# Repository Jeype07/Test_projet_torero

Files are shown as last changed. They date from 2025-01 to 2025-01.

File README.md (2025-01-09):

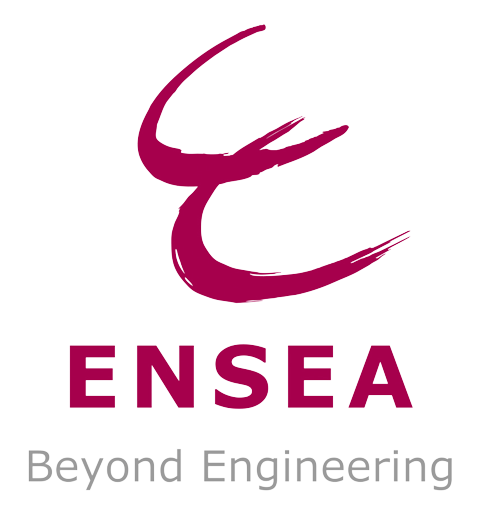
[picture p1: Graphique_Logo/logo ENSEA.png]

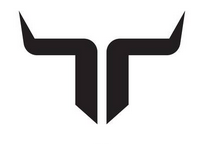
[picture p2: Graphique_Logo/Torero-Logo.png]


# 2425_ESE_Projet_Torero

## Projet de ESE de 3éme année de JACQUOT Nolan, GUIFFAULT Gabriel, BOULOT Paul et THOMAR Jean-Philippe

Ce projet contient toute les ressources de l'élaboration d'un robot capable de jouer au chat et a la souris.
Les liens vers les differentes ressources sont énuméré avec un court intitulé a la FIN du README.
Ci dessous le schéma architectural donnant les grandes lignes du projet.
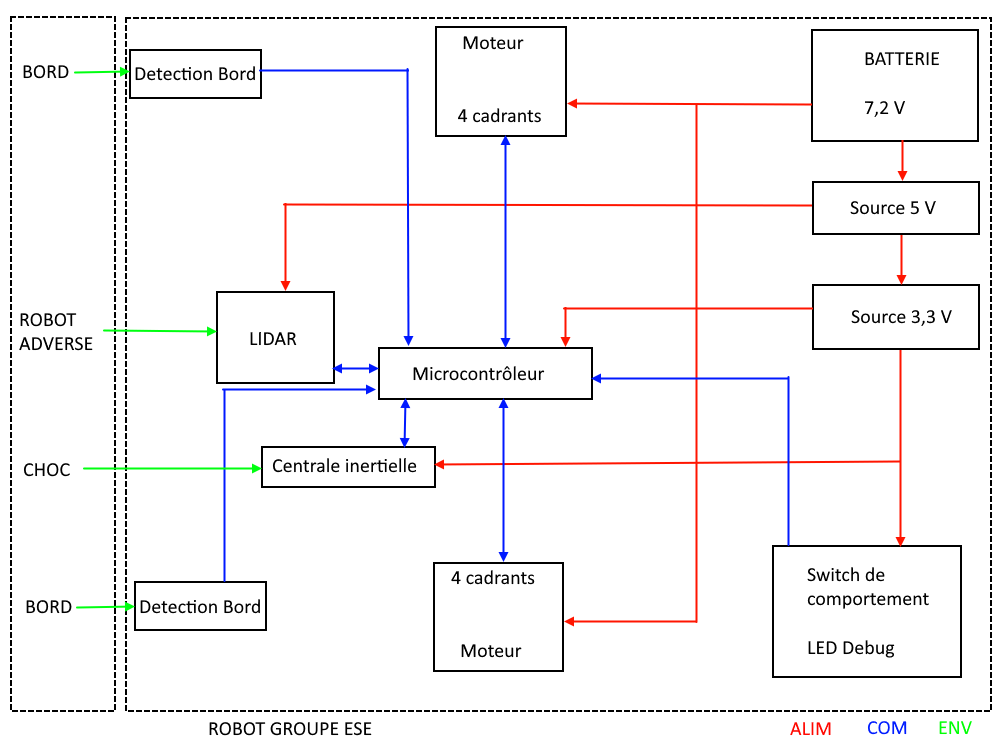
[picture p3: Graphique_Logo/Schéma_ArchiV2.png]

[Schéma architectural](https://github.com/user-attachments/files/17220902/Schema.architectural.pdf)

## Environnement:

> [!IMPORTANT]
> Table de 200cm x 160cm
> 
> Table sans Bord ni marquages!
> 
> Robot assimilable a un cylindre de 17 cm de diametre et 15 cm de hauteur 

## Cahier des charges:
> [!IMPORTANT]
>- Le robot doit etre capable de ce déplacer sur une table sans tomber (absence de bord et de marquage)
>- Le robot doit etre capable de detecter l'autre robot present sur la table pour le fuir ou le chasser en fonction de son role dans la partie.
>- Le robot doit etre capable de detecter un contact meme leger avec le robot adverse et changer son comportement d'un role vers l'autre.

Objectif annexe:
- Le robot peut realiser une odometrie simple pour suivre le bord de table lorsqu'il debute en souris
- Le robot peut realiser une odometrie simple pour se positionner au centre de la table avant de commencer la traque lorsqu'il debute en chat
- Le robot peut declencher un brusque changement de direction si il detecte un robot approchant rapidement en mode souris
- Le robot peut effectuer des prédiction de trajectoire et effectuer des trajectoires de collision en prévision du deplacement adverse en mode chat
- Le robot evite de prendre des directions ou il serait acculé dans un angle de table

### Dossier contenant les Datasheets : 
https://github.com/Manassehalt/2425_ESE_Projet_Torero/tree/main/Datasheet

### LISTE des choses faite ou a faire : 
https://github.com/Manassehalt/2425_ESE_Projet_Torero/blob/main/Calculs%20et%20brouillons/Remarque_Sch.md

### Lien utile : 
https://github.com/Manassehalt/2425_ESE_Projet_Torero/blob/main/Calculs%20et%20brouillons/Liens.xlsx

### BOM : 
https://github.com/Manassehalt/2425_ESE_Projet_Torero/blob/main/BOM.xlsx

### INFO PCB : 
https://github.com/Manassehalt/2425_ESE_Projet_Torero/blob/main/PCB/info_PCB.docx

### Apercu serigraphie :
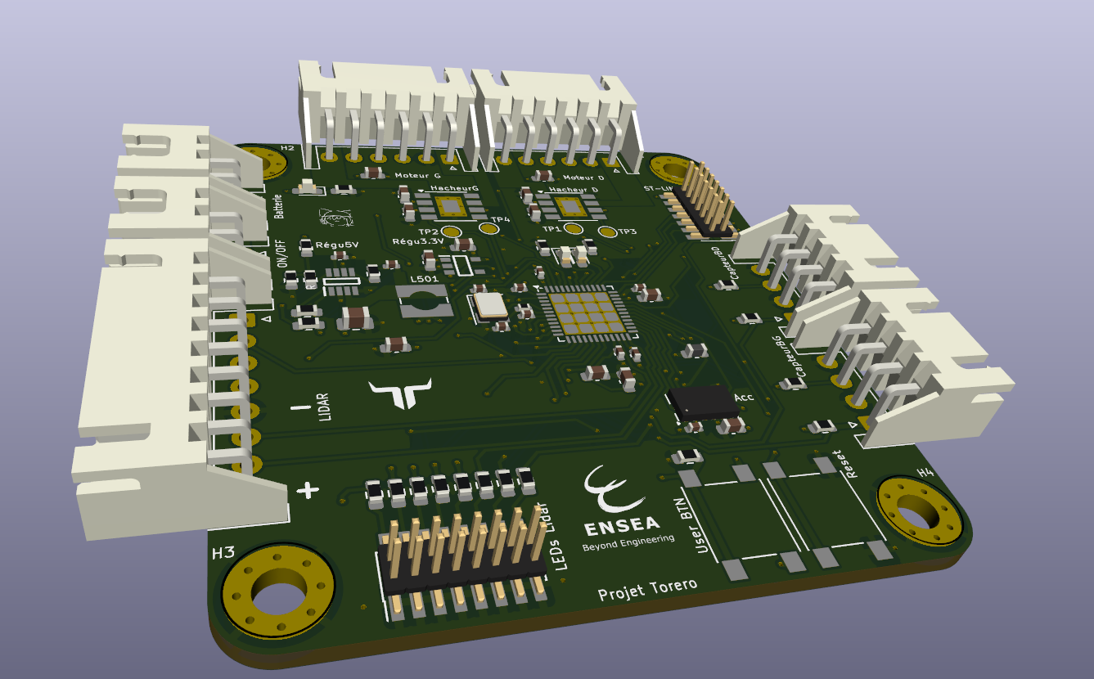
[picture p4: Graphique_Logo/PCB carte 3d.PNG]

[view PCB 3D](https://github.com/Manassehalt/2425_ESE_Projet_Torero/blob/main/Graphique_Logo/PCB%20carte%203d.PNG)

### DOSSIER PCB : 
https://github.com/Manassehalt/2425_ESE_Projet_Torero/tree/main/PCB

### Shematics_torero : 
https://github.com/Manassehalt/2425_ESE_Projet_Torero/blob/main/PCB/Projet_torero/Projet_torero.kicad_sch

### DOSSIER CODE STM32 : 
https://github.com/Manassehalt/2425_ESE_Projet_Torero/tree/main/Projet_ESE_STM32/Projet_ESE_Torero/STM32G431CBU6

### DOSSIER CALCULS : 
https://github.com/Manassehalt/2425_ESE_Projet_Torero/tree/8892ed05e16a1e8a040fe9dc08f9f57ab23dc9e8/Calculs%20et%20brouillons

### Methode si nouvel ordinateur : 
> [!TIP]
>Générer une clé SSH
>- Taper ssh-keygen puis Entrer
>- Appuyer sur y pour overwrite et sur Entrer pour passer les étapes (if no passphrase)
>- Taper cat ~/.ssh/id_ed25519.pub puis Entrer
>- Copier puis coller la clé dans GitHub Setting > SSH and GPG keys > SSH keys
>- Renommer avec le nom du PC pour savoir à quoi la clé correpond
>  ex : jeanp@HP-Pavilion-JP

### Ligne pour cloner un répertoire en utilisant le port 443 (https) au lieu du port 22, si bug sur la connexion:
> [!TIP]
>git clone ssh://git@ssh.github.com:443/username/Repositority_name.git

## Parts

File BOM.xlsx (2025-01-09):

NOM | REFERENCE | FOURNISSEUR | DESCRIPTION | PRIX UNITAIRE | QUANTITE | COUT TOTAL | STATUS COMMANDE | DATASHEET
STM32G431CBU6 |  |  | Microcontrôleur |  | 1 | 0.00 €
Quartz 16 MHz | 2853935 | Farnell |  |  | 1 | 0.00 €
Connecteur SWD/STLink | 3226055 | Farnell |  |  |  | 0.00 €
ZXBM5210-SP-13 |  |  | Driver moteur |  |  | 0.00 €
DfRobot FIT0520 ou FIT0521 |  |  | Moteurs |  | 2 | 0.00 €
ADXL343BCCZ-RL |  |  | Accéléromètre |  | 1 | 0.00 €
MP1475S |  |  | Régulateur 5V |  | 1 | 0.00 €
BU33SD5WG-TR |  |  | Régulateur 3.3V |  | 1 | 0.00 €
NIMH 7.2V 1.3Ah (RS : 777-0377) |  |  | Batterie 7.2V |  |  | 0.00 €
QRD1113 | 1467857/1467858 | Farnell | Capteur bordure |  | 2 | 0.00 €
YDLIDAR X4 |  |  | Lidar |  | 1 | 0.00 €
Connecteurs JST 2.54mm |  |  |  |  |  | 0.00 €
LED + R/C |  |  |  |  |  | 0.00 € | en 0603
Résistance 10 k |  |  | Résistance boot flash user button |  | 1
Capacité 20p |  |  |  |  | 2
Capacité 100n |  |  |  |  | 8
Capacité 1u |  |  |  |  | 9
Capacité 4n7 |  |  |  |  | 1
Capacité 10n |  |  |  |  | 1
Capacité 22u |  |  |  |  | 1
Capacité 47u |  |  |  |  | 1
Capacité 10u |  |  |  |  | 2
Diode rouge |  |  |  |  | 2
Diode verte |  |  |  |  | 1
Connecteur Pin header 2x7 1,27mm ST Link |  |  |  |  | 1
Connecteur Pin header 2x8 1,27mm debug Lidar |  |  |  |  | 1
Connecteur JST 1x8 2,5mm Lidar |  |  |  |  | 1
Connecteurs JST 1x 2 2,5mm (batterie + switch) |  |  |  |  | 2
Connecteur JST 1x6 2,5mm moteur |  |  |  |  | 2
Inductance passe bas VDDA stm32 |  |  |  |  | 1
Inductance 4u7 |  |  | Régulateur tension 5V |  | 1
Résistance 10 |  |  |  |  | 1
Résistance 120 |  |  |  |  | 1
Résistance 140 |  |  |  |  | 2
Résistance 1k |  |  |  |  | 8
Résistance 100k |  |  |  |  | 2
Résistance 20 |  |  |  |  | 1
Résistance 16k |  |  |  |  | 1
Résistance 40k2 |  |  |  |  | 1
Résistance 7k68 |  |  |  |  | 1
Résistance 300 |  |  |  |  | 2
Résistance 15k3 |  |  |  |  | 2
Switch push |  |  | stm32 NRST et Boot Flash |  | 2

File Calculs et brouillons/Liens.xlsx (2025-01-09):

DESCRIPTION | LIENS
Guide pour les calculs et branchement du capteur de bord QRD1113/14(attention arduino) | https://learn.sparkfun.com/tutorials/qrd1114-optical-detector-hookup-guide/all
Current Limiting Resistor: Protective Resistor for Regulating Current (for QRD1113/14) | https://www.ourpcb.com/current-limiting-resistor.html

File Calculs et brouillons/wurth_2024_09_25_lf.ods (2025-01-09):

Value | Footprint | Tension | Qty | Wuerth
100nF | 402 | 25 | 1000 | 885012205085
15pF | 402 | 50 | 100 | 885012005056
10pF | 402 | 50 | 1000 | 885012005055
1uF | 603 | 25 | 1000 | 885012206076
10nF | 402 | 50 | 1000 | 885012205067
4.7uF | 603 | 10 | 1000 | 885012106012
22uF | 805 | 25 | 1000 | 885012107019
10uF | 603 | 25 | 1000 | 885012106031
6.8uH | >2A |  | 100 | 74404054068
4.7uH | >2A |  | 100 | 74404052047

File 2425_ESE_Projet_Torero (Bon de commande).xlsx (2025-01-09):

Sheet: Farnell
Farnell |  |  |  |  | Envoyez un seul fichier par mail!
Pos | I | P | Art | Désignation | Qté commandée | UA | Date Livraison | Prix unitaire | Devise | Q | Grpe | Div
10 | Z |  |  | 1467857 Capteur bordure QRD1113 | 4 | PC |  | 2.09 | EUR | PC | TA.01
20 | Z |  |  |  |  | PC |  |  | EUR | PC | TA.01
30 | Z |  |  |  |  | PC |  |  | EUR | PC | TA.01
40 | Z |  |  |  |  | PC |  |  | EUR | PC | TA.01
50 | Z |  |  |  |  | PC |  |  | EUR | PC | TA.01
60 | Z |  |  |  |  | PC |  |  | EUR | PC | TA.01
70 | Z |  |  |  |  | PC |  |  | EUR | PC | TA.01
80 | Z |  |  |  |  | PC |  |  | EUR | PC | TA.01
90 | Z |  |  |  |  | PC |  |  | EUR | PC | TA.01
100 | Z |  |  |  |  | PC |  |  | EUR | PC | TA.01
110 | Z |  |  |  |  | PC |  |  | EUR | PC | TA.01
120 | Z |  |  |  |  | PC |  |  | EUR | PC | TA.01
130 | Z |  |  |  |  | PC |  |  | EUR | PC | TA.01
140 | Z |  |  |  |  | PC |  |  | EUR | PC | TA.01
150 | Z |  |  |  |  | PC |  |  | EUR | PC | TA.01
160 | Z |  |  |  |  | PC |  |  | EUR | PC | TA.01
170 | Z |  |  |  |  | PC |  |  | EUR | PC | TA.01
180 | Z |  |  |  |  | PC |  |  | EUR | PC | TA.01
190 | Z |  |  |  |  | PC |  |  | EUR | PC | TA.01
MODE d'EMPLOI et CODE erreurs Version 19
1: indiquez le fournisseur ligne 1
2:remplissez pour chaque ligne commandée les 4 champs en rouge selon les règles suivantes:
 | Art
 |  |  | 2.1 | Ne mettez rien ici tout comme dans P: remplissez les zones rouges (et pas ailleurs)
 | Désignation
 |  |  | 2.2 | Ne dépassez pas les 40 caractères: il seront automatiquement effacés lors de la recopie
 |  |  | 2.3 | Mettre le code commande impérativement en premier suivi d'une courte description
 |  |  | 2.4 | Pour RS et Farnell : mettre le code commande RS ou Farnell (7 à 9 chiffres) (et pas la référence constructeur) suivie d'une courte description
 |  |  | 2.5 | Exemple: 125-4857 capa 1uF 0508
 | Qté commandée
 |  |  | 2.6 | C'est le nombre d'unités correspondant au prix unitaire
 |  |  | 2.7 | Attention il y a des pièges
 |  |  | 2.8 | avec RS par exemple on vous demande parfois de commander par lot de 5 par exemple
 |  |  | 2.9 | si vous commandez 1 lot : le nombre d'unité est alors 5 pour 1 lot et non 1
 | date
 |  |  | 2.10 | Pour la date: mettre la de date dans une semaine
 |  |  | 2.11 | La mettre au format JJ.MM.AAAA
 |  |  | 2.13 | Bien utiliser les points comme séparateur
 | prix unitaire
 |  |  | 2.14 | Le prix est le prix HT (sans la TVA 20%) en euros d'une unité | sauf pour les commandes au comptant ou chez un fournisseur étranger (EXP-TECH par exemple): mettez le prix TTC
 |  |  | 2.15 | arrondi au centime supérieur (0.012 euros devient 0.02!)
 |  |  | 2.16 | avec pour séparateur le point
 |  |  | 2.17 | n'utilisez pas le symbole euros d'excel
3: frais de port
 |  |  | 3.1 | ajoutez une ligne pour les frais de port
 |  |  | 3.2 | dont la désignation est "frais de port"
 |  |  | 3.3 | pas de frais de port à mettre pour RS ou Farnell
 |  |  | 3.4 | Renseignez vous pour connaître les frais de port | 9,9 euros TTC chez EXP par exemple
4: conseils complémentaires
 |  |  | 4.1 | Ne modifier que les 4 champs en rouge
 |  |  | 4.2 | Ne pas modifier le document sinon cela n'a plus aucun intérêt
 |  |  | 4.3 | Mettez les références dans le même ordre que celui de la commande
 |  |  | 4.4 | Vérifier bien sur les sites les références et les prix!
 |  |  | 4.5 | N'oubliez pas les frais de port!: ajoutez une ligne pour les mentionner
5: sauvegardez le fichier au format xls

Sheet: RS
RS |  |  |  |  | Envoyez un seul fichier par mail!
Pos | I | P | Art | Désignation | Qté commandée | UA | Date Livraison | Prix unitaire | Devise | Q | Grpe | Div
10 | Z |  |  | 820-1605 Connecteur JST 1x8 2,5mm | 5 | PC |  | 0.3 | EUR | PC | TA.01
20 | Z |  |  | 515-1349 connecteur JST 1x6 2,5mm | 10 | PC |  | 0.27 | EUR | PC | TA.01
30 | Z |  |  | 820-1582 connecteur JST 1x2 2,5mm | 5 | PC |  | 0.27 | EUR | PC | TA.01
40 | Z |  |  | 479-1435 switch push button 6 x 6 x 9.5mm | 20 | PC |  | 0.15 | EUR | PC | TA.01
50 | Z |  |  | 828-1866 connecteur pin header 2x8 1,27mm | 5 | PC |  | 2.05 | EUR | PC | TA.01
60 | Z |  |  | 828-1862 connecteur pin header 2x7 1,27mm | 5 | PC |  | 1.54 | EUR | PC | TA.01
70 | Z |  |  |  |  | PC |  |  | EUR | PC | TA.01
80 | Z |  |  |  |  | PC |  |  | EUR | PC | TA.01
90 | Z |  |  |  |  | PC |  |  | EUR | PC | TA.01
100 | Z |  |  |  |  | PC |  |  | EUR | PC | TA.01
110 | Z |  |  |  |  | PC |  |  | EUR | PC | TA.01
120 | Z |  |  |  |  | PC |  |  | EUR | PC | TA.01
130 | Z |  |  |  |  | PC |  |  | EUR | PC | TA.01
140 | Z |  |  |  |  | PC |  |  | EUR | PC | TA.01
150 | Z |  |  |  |  | PC |  |  | EUR | PC | TA.01
160 | Z |  |  |  |  | PC |  |  | EUR | PC | TA.01
170 | Z |  |  |  |  | PC |  |  | EUR | PC | TA.01
180 | Z |  |  |  |  | PC |  |  | EUR | PC | TA.01
190 | Z |  |  |  |  | PC |  |  | EUR | PC | TA.01
MODE d'EMPLOI et CODE erreurs Version 19
1: indiquez le fournisseur ligne 1
2:remplissez pour chaque ligne commandée les 4 champs en rouge selon les règles suivantes:
 | Art
 |  |  | 2.1 | Ne mettez rien ici tout comme dans P: remplissez les zones rouges (et pas ailleurs)
 | Désignation
 |  |  | 2.2 | Ne dépassez pas les 40 caractères: il seront automatiquement effacés lors de la recopie
 |  |  | 2.3 | Mettre le code commande impérativement en premier suivi d'une courte description
 |  |  | 2.4 | Pour RS et Farnell : mettre le code commande RS ou Farnell (7 à 9 chiffres) (et pas la référence constructeur) suivie d'une courte description
 |  |  | 2.5 | Exemple: 125-4857 capa 1uF 0508
 | Qté commandée
 |  |  | 2.6 | C'est le nombre d'unités correspondant au prix unitaire
 |  |  | 2.7 | Attention il y a des pièges
 |  |  | 2.8 | avec RS par exemple on vous demande parfois de commander par lot de 5 par exemple
 |  |  | 2.9 | si vous commandez 1 lot : le nombre d'unité est alors 5 pour 1 lot et non 1
 | date
 |  |  | 2.10 | Pour la date: mettre la de date dans une semaine
 |  |  | 2.11 | La mettre au format JJ.MM.AAAA
 |  |  | 2.13 | Bien utiliser les points comme séparateur
 | prix unitaire
 |  |  | 2.14 | Le prix est le prix HT (sans la TVA 20%) en euros d'une unité | sauf pour les commandes au comptant ou chez un fournisseur étranger (EXP-TECH par exemple): mettez le prix TTC
 |  |  | 2.15 | arrondi au centime supérieur (0.012 euros devient 0.02!)
 |  |  | 2.16 | avec pour séparateur le point
 |  |  | 2.17 | n'utilisez pas le symbole euros d'excel
3: frais de port
 |  |  | 3.1 | ajoutez une ligne pour les frais de port
 |  |  | 3.2 | dont la désignation est "frais de port"
 |  |  | 3.3 | pas de frais de port à mettre pour RS ou Farnell
 |  |  | 3.4 | Renseignez vous pour connaître les frais de port | 9,9 euros TTC chez EXP par exemple
4: conseils complémentaires
 |  |  | 4.1 | Ne modifier que les 4 champs en rouge
 |  |  | 4.2 | Ne pas modifier le document sinon cela n'a plus aucun intérêt
 |  |  | 4.3 | Mettez les références dans le même ordre que celui de la commande
 |  |  | 4.4 | Vérifier bien sur les sites les références et les prix!
 |  |  | 4.5 | N'oubliez pas les frais de port!: ajoutez une ligne pour les mentionner
5: sauvegardez le fichier au format xls

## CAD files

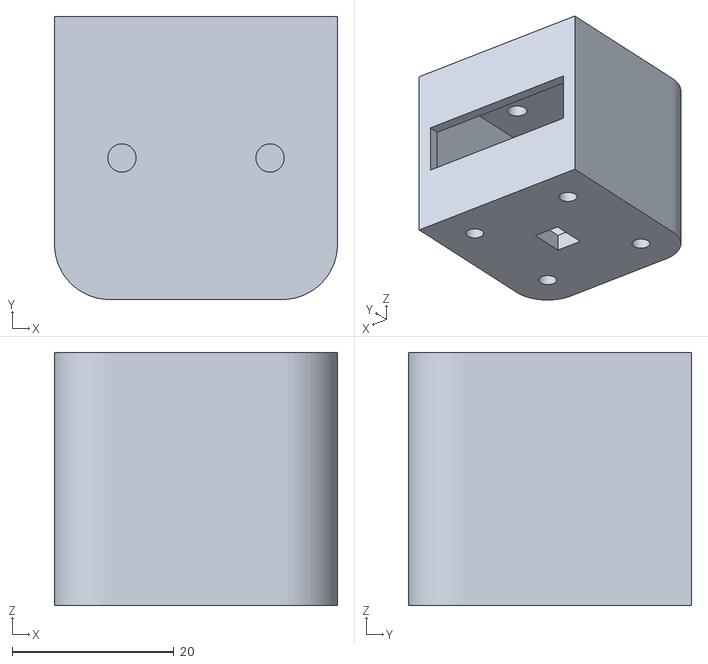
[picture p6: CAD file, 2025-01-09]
Meca/SupportCapteur.stl
35.0 x 35.0 x 31.4

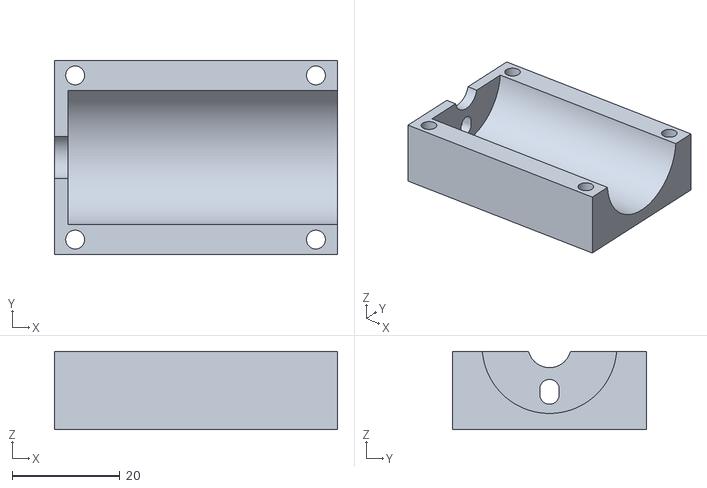
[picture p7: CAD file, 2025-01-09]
Meca/SupportMotor.stl
52.5 x 36.0 x 14.5

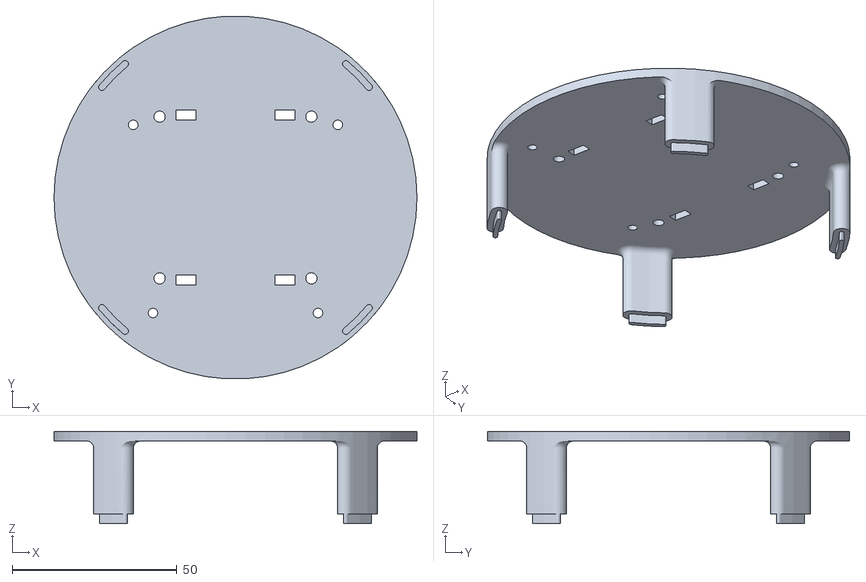
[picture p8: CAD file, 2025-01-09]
Meca/Tower.stl
110.0 x 109.8 x 28.0

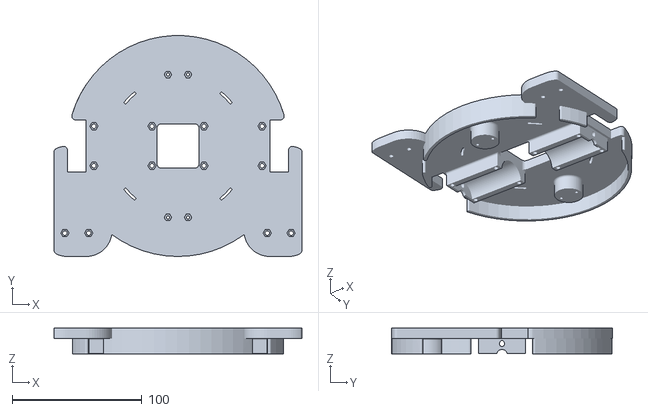
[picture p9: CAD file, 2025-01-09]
Meca/Base.stl
190.8 x 170.0 x 20.0

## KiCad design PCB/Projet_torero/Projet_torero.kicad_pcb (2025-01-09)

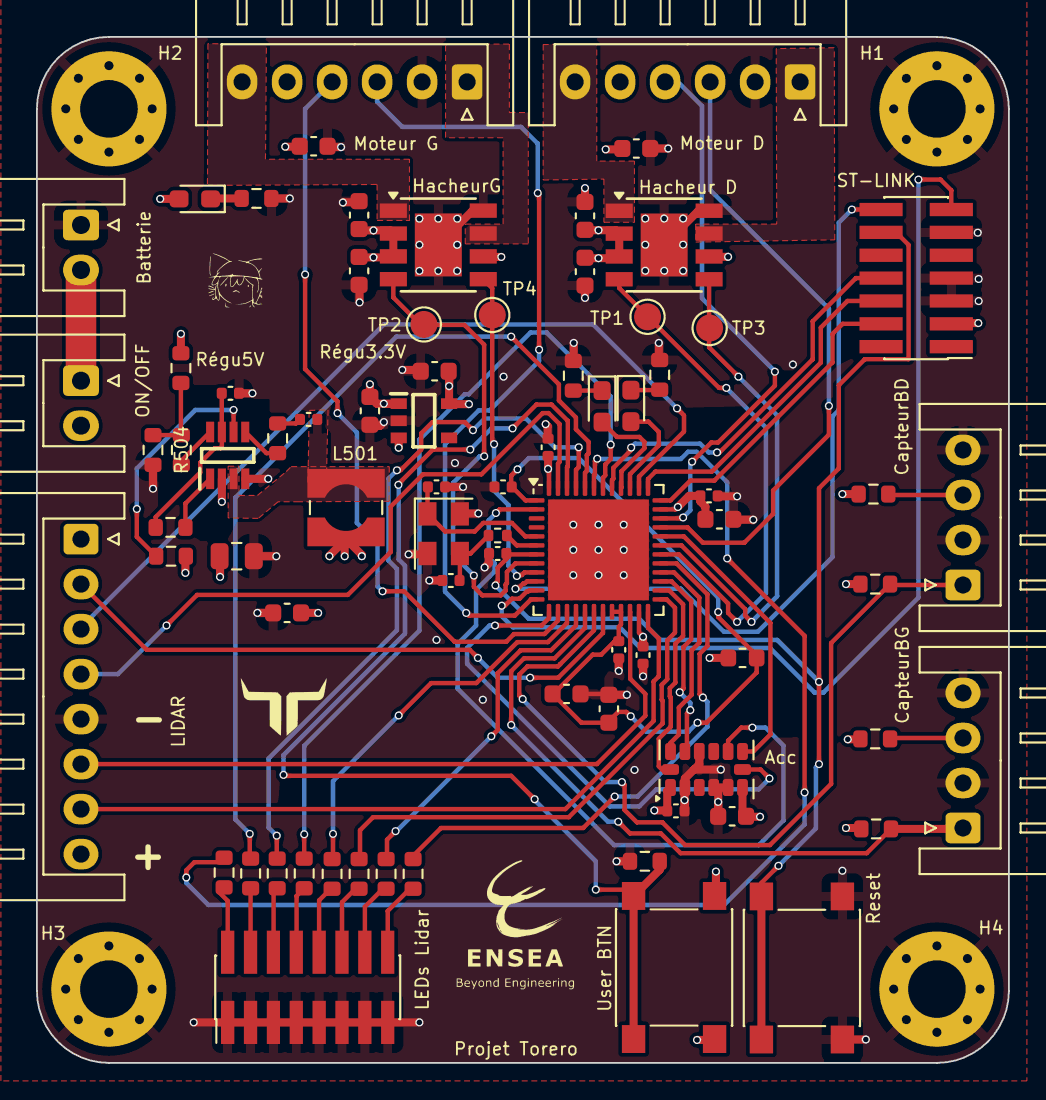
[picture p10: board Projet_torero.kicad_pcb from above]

Board: 4 copper layers, 54.0 x 57.0 mm, 79 parts (0 on the bottom side), 72 nets.

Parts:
10k201: 10k; R_0603_1608Metric
Acc: ADXL343; LGA-14_3x5mm_P0.8mm_LayoutBorder1x6y
Batterie: Conn_01x02; JST_XH_S2B-XH-A_1x02_P2.50mm_Horizontal
C201, C202: 20p; C_0402_1005Metric
C203, C204, C206, C207, C208, C402, C502, C503: 100n; C_0402_1005Metric
C205, C210, C401, C505, C506, C601, C603, C701, C703: 1u; C_0603_1608Metric
C209: 4n7; C_0603_1608Metric
C211: 10n; C_0402_1005Metric
C501: 22u; C_0805_2012Metric
C504: 47u; C_0603_1608Metric
C602, C702: 10u; C_0603_1608Metric
CapteurBD: JST_XH_S4B-XH-A_1x04_P2.50mm_Horizontal
CapteurBG: JST_XH_S4B-XH-A_1x04_P2.50mm_Horizontal
D1, D202: Red; LED_0603_1608Metric_Pad1.05x0.95mm_HandSolder
D201: Green; LED_0603_1608Metric_Pad1.05x0.95mm_HandSolder
H1, H2, H3, H4: MountingHole_Pad; MountingHole_3.2mm_M3_Pad_Via
Hacheur D: ZXBM5210-SP; Diodes_SO-8EP
HacheurG: ZXBM5210-SP; Diodes_SO-8EP
L202: L; L_0603_1608Metric
L501: 4u7; L_Wuerth_WE-TPC-3816
LEDs Lidar: Conn_02x08_Odd_Even; PinHeader_2x08_P1.27mm_Vertical_SMD
LIDAR: Conn_01x08; JST_XH_S8B-XH-A_1x08_P2.50mm_Horizontal
Moteur D: Conn_01x06; JST_XH_S6B-XH-A_1x06_P2.50mm_Horizontal
Moteur G: Conn_01x06; JST_XH_S6B-XH-A_1x06_P2.50mm_Horizontal
ON/OFF: Conn_01x02; JST_XH_S2B-XH-A_1x02_P2.50mm_Horizontal
R201: 10; R_0402_1005Metric
R202: 120; R_0603_1608Metric
R203, R314: 140; R_0603_1608Metric
R204, R205, R206, R207, R208, R209, R210, R211: 1k; R_0603_1608Metric
R501, R502: 100k; R_0603_1608Metric
R503: 20; R_0603_1608Metric
R504: 16k; R_0603_1608Metric
R505: 40k2; R_0603_1608Metric
R506: 7k68; R_0603_1608Metric
R801, R901: 300; R_0603_1608Metric
R802, R902: 15k3; R_0603_1608Metric
Reset: SW_Push; SW_Push_1P1T_NO_6x6mm_H9.5mm
Régu3.3V: BU33SD5WG-TR; SOT95P280X125-5N
Régu5V: MP1475SGJ-P; SOT65P280X100-8N
ST-LINK: Conn_02x07_Odd_Even; PinHeader_2x07_P1.27mm_Vertical_SMD
SW201: SW_Push; SW_Push_1P1T_NO_6x6mm_H9.5mm
TP1, TP2, TP3, TP4: TestPoint; TestPoint_Pad_D1.5mm
U201: STM32G431CBUx; QFN-48-1EP_7x7mm_P0.5mm_EP5.6x5.6mm
Y201: Crystal_GND24_Small; Crystal_SMD_EuroQuartz_MT-4Pin_3.2x2.5mm

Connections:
7.2V: C501.1, C601.2, C602.1, C701.2, C702.1, Hacheur D.2 (VM), Hacheur D.3 (VDD), Hacheur D.6 (VREF), HacheurG.2 (VM), HacheurG.3 (VDD), HacheurG.6 (VREF), ON/OFF.2, R501.1, Régu5V.2 (IN)
+3.3V: Acc.1 (Vdd_I/O), Acc.6 (Vs), C206.1, C207.1, C208.1, C209.1, C401.1, C402.2, C506.2, C603.2, C703.2, D201.2 (A), L202.1, Moteur D.5, Moteur G.5, R801.1, R802.2, R901.1, R902.2, Régu3.3V.5 (VOUT), ST-LINK.3, SW201.2, U201.23 (VDD), U201.35 (VDD), U201.48 (VDD)
+5V: C504.1, C505.1, L501.2, LIDAR.8, R505.1, Régu3.3V.1 (VIN), Régu3.3V.3 (STBY)
/ALIMENTATION/Sortie Régulateur 5V: C503.2, L501.1, Régu5V.3 (SW)
/CAPTEURS/ANALOG_OUTPUT_CAPT_BORD_D: CapteurBD.1, R901.2, U201.18 (PB1)
/CAPTEURS/ANALOG_OUTPUT_CAPT_BORD_G: CapteurBG.1, R801.2, U201.17 (PB0)
/CAPTEURS/CS_ACC: Acc.7 (~CS), U201.13 (PA5)
/CAPTEURS/DEV_EN_LIDAR: LIDAR.3, U201.38 (PA15)
/CAPTEURS/INT1_ACC: Acc.8 (INT1), U201.32 (PA10)
/CAPTEURS/INT2_ACC: Acc.9 (INT2), U201.2 (PC13)
/CAPTEURS/M_EN_LIDAR: LIDAR.2, U201.19 (PB2)
/CAPTEURS/M_SCTR_LIDAR: LIDAR.4, U201.47 (PB9)
/CAPTEURS/Rx_LIDAR: LIDAR.6, U201.22 (PB10)
/CAPTEURS/SCLK_ACC: Acc.14 (SCL/SCLK), U201.26 (PB13)
/CAPTEURS/SDI_ACC: Acc.13 (SDA/SDI/SDIO), U201.28 (PB15)
/CAPTEURS/SDO_ACC: Acc.12 (SDO/ADDR), U201.27 (PB14)
/CAPTEURS/Tx_LIDAR: LIDAR.7, U201.24 (PB11)
/PUISSANCE/EncodeurA_Droite: Moteur G.3, U201.12 (PA4)
/PUISSANCE/EncodeurA_Gauche: Moteur D.3, U201.33 (PA11)
/PUISSANCE/EncodeurB_Droite: Moteur G.4, U201.14 (PA6)
/PUISSANCE/EncodeurB_Gauche: Moteur D.4, U201.34 (PA12)
/PUISSANCE/FWDD: HacheurG.4 (FWD), TP2.1, U201.8 (PA0)
/PUISSANCE/FWDG: Hacheur D.4 (FWD), TP1.1, U201.30 (PA8)
/PUISSANCE/Moteur1/Commande moteur: HacheurG.7 (OUT2), Moteur G.1
/PUISSANCE/Moteur1/Connecteur Moteur: HacheurG.1 (OUT1), Moteur G.6
/PUISSANCE/Moteur/Commande moteur: Hacheur D.7 (OUT2), Moteur D.1
/PUISSANCE/Moteur/Connecteur Moteur: Hacheur D.1 (OUT1), Moteur D.6
/PUISSANCE/REVD: HacheurG.5 (REV), TP4.1, U201.9 (PA1)
/PUISSANCE/REVG: Hacheur D.5 (REV), TP3.1, U201.31 (PA9)
/STM32/USER_BTN: 10k201.2, SW201.1, U201.46 (PB8)
GND: 10k201.1, Acc.2 (GND), Acc.4 (GND), Acc.5 (GND), Acc.11 (RES), Batterie.1, C201.1, C202.2, C203.2, C204.2, C205.2, C206.2, C207.2, C208.2, C209.2, C210.2, C211.2, C401.2, C402.1, C501.2, C502.2, C504.2, C505.2, C506.1, C601.1, C602.2, C603.1, C701.1, C702.2, C703.1, CapteurBD.2, CapteurBD.4, CapteurBG.2, CapteurBG.4, H1.1, H2.1, H3.1, H4.1, Hacheur D.8 (GND), Hacheur D.9 (GND), HacheurG.8 (GND), HacheurG.9 (GND), LEDs Lidar.1, LEDs Lidar.3, LEDs Lidar.5, LEDs Lidar.7, LEDs Lidar.9, LEDs Lidar.11, LEDs Lidar.13, LEDs Lidar.15, LIDAR.5, Moteur D.2, Moteur G.2, R202.1, R203.1, R314.1, R506.2, Reset.1, Régu3.3V.2 (GND), Régu5V.4 (GND), ST-LINK.5, ST-LINK.7, ST-LINK.11, U201.49 (VSS), Y201.2, Y201.4
LED_E: R205.1, U201.44 (PB6)
LED_N: R204.1, U201.43 (PB5)
LED_NE: R208.1, U201.15 (PA7)
LED_NW: R209.1, U201.25 (PB12)
LED_S: R206.1, U201.45 (PB7)
LED_SE: R210.1, U201.16 (PC4)
LED_SW: R211.1, U201.29 (PC6)
LED_W: R207.1, U201.42 (PB4)
NRST: C203.1, Reset.2, ST-LINK.12, U201.7 (PG10)
unnamed: C201.2, R201.2, Y201.3
unnamed: C503.1, R503.1
unnamed: D1.1 (K), R314.2
unnamed: D201.1 (K), R202.2
unnamed: D202.1 (K), R203.2
unnamed: R503.2, Régu5V.5 (BST)
unnamed: R501.2, Régu5V.6 (EN/SYNC)
unnamed: R504.2, Régu5V.8 (FB)
unnamed: R502.2, Régu5V.1 (PG)
unnamed: C502.1, R502.1, Régu5V.7 (VCC)
unnamed: LEDs Lidar.2, R204.2
unnamed: LEDs Lidar.4, R205.2
unnamed: LEDs Lidar.6, R206.2
unnamed: LEDs Lidar.8, R207.2
unnamed: LEDs Lidar.10, R208.2
unnamed: LEDs Lidar.12, R209.2
unnamed: LEDs Lidar.14, R210.2
unnamed: LEDs Lidar.16, R211.2
unnamed: Batterie.2, ON/OFF.1
unnamed: CapteurBG.3, R802.1
unnamed: CapteurBD.3, R902.1
unnamed: R504.1, R505.2, R506.1
unnamed: C202.1, U201.5 (PF0), Y201.1
unnamed: R201.1, U201.6 (PF1)
unnamed: C204.1, C205.1, C210.1, C211.1, L202.2, U201.1 (VBAT), U201.20 (VREF+), U201.21 (VDDA)
STATUS_LED: D202.2 (A), U201.39 (PC10)
STATUS_LED_Debug: D1.2 (A), U201.40 (PC11)
SWCLK: ST-LINK.6, U201.37 (PA14)
SWDIO: ST-LINK.4, U201.36 (PA13)
SWO: ST-LINK.8, U201.41 (PB3)
VCP_RX: ST-LINK.13, U201.11 (PA3)
VCP_TX: ST-LINK.14, U201.10 (PA2)

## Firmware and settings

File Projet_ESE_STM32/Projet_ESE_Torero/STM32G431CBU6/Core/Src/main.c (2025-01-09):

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
/* Includes ------------------------------------------------------------------*/
#include "main.h"
#include "cmsis_os.h"
#include "dma.h"
#include "spi.h"
#include "tim.h"
#include "usart.h"
#include "gpio.h"

/* USER CODE BEGIN Includes */
#include "ydlidarx4_header.h"
#include "stdio.h"
#include "ADXL.h"
#include "motor.h"
/* USER CODE END Includes */

/* USER CODE BEGIN PTD */
#define ADXL343_CS_GPIO GPIOA
#define ADXL343_CS_PIN GPIO_PIN_5
#define PWM_MAX_DUTY_CYCLE 8499
#define FWD_GPIO_PIN GPIO_PIN_8  // PA8 -> FWD
#define REV_GPIO_PIN GPIO_PIN_9  // PA9 -> REV
#define FWD_GPIO_PORT GPIOA      // Port pour FWD
#define REV_GPIO_PORT GPIOA      // Port pour REV
#define UART_RX_BUFFER_SIZE 1
#define UART_TX_BUFFER_SIZE 64

#define STACK_SIZE 256

#define SHOCK_THRESHOLD 15
/* USER CODE END PTD */

/* USER CODE BEGIN PM */
LIDAR_HandleTypeDef_t hlidar;

SemaphoreHandle_t SemHalfCallBack;
SemaphoreHandle_t SemClpCallBack;

TaskHandle_t xHandleLIDAR = NULL;
TaskHandle_t xHandleETAT = NULL;
TaskHandle_t xHandleACC = NULL;
TaskHandle_t xHandleMOTOR = NULL;
TaskHandle_t xHandleEDGE = NULL;
//TaskHandle_t xHandleMOTOR = NULL;
BaseType_t ret;
/* USER CODE END PM */


void SystemClock_Config(void);
void MX_FREERTOS_Init(void);
/* USER CODE BEGIN PFP */
void TaskMOTOR (void * pvParameters);
void TaskETAT(void * pvParameters);
void TaskLIDAR(void * pvParameters);
/* USER CODE END PFP */

/* USER CODE BEGIN 0 */

//flag choc
int shock_detected = 0;

//flag caoteurs bord
int capteur_G = 0;
int capteur_D = 0;
int capteur_virtuel = 0;

//Vitesse
int angle;		//Calcul de alpha
int vitesse;	//

//Etat Robot
int chat = 0;	//0 -> souris	1 -> chat
int alpha1,alpha2;
float coeff_Lidar, coeff_Capteur;
float delta;
SemaphoreHandle_t SemEtat;
SemaphoreHandle_t SemEdge;
SemaphoreHandle_t xShockSemaphore;
//SemaphoreHandle_t xNoSignalSemaphore;
SemaphoreHandle_t SemDMAHalfCallBack;
SemaphoreHandle_t SemDMAClpCallBack;

//Lidar
int distance_min=0;
int idx_min = 0;
int frame_start = 0;
int frame_end = 0;



int __io_putchar(int chr){
	HAL_UART_Transmit(&huart2, (uint8_t*)&chr, 1, HAL_MAX_DELAY);
	return chr;
}

void print_buffer(const char * Name, uint8_t *pData, uint16_t Size, int N_lines){
	printf("%s", Name);
	if(N_lines >= (int) Size){
		for(int i = 0; i<Size; i++){
			printf("%d : %d\r\n", i, pData[i]);
		}
	}
	else{
		for(int i = 0; i<N_lines; i++){
			printf("%d : %d\r\n", i, pData[i]);
		}
	}
}

void TaskETAT(void * pvParameters){
	for (;;) {
		// Attendre que la notification arrive
		printf("hi\r\n");
		ulTaskNotifyTake(pdTRUE, portMAX_DELAY);
		//lire INT_SOURCEmet à 0 bit interruption single tap pour générer une nouvelle interruption au prochain tap
		uint8_t rst_int = SPI_Read(ADXL343_REG_INT_SOURCE);
		if(chat == 1){
			chat = 0;
			printf("Squik\r\n");
		}
		else{
			// Le choc a été détecté
			chat = 1;
			printf("Miaou\r\n");
		}
	}

}

void TaskLIDAR(void * pvParameters){
	for(;;){
		printf("lidar\r\n");
		vTaskDelay(100);
	}
}

void TaskMOTOR (void * pvParameters){
	for(;;){

		Motor_Forward_R(50);
		Motor_Forward_L(50);
		Motor_Forward_R(80);
		Motor_Forward_L(80);
	}
}

/*		Début de comportement à implementer pour asserv dynamique
 *
 * 		capteur_virtuel = capteur_G&&capteur_D;
		int erreur_capteur = -45*capteur_G+45*capteur_D+90*capteur_virtuel;
		int erreurLidar = 10/180;
		int alphaD = coeff_Lidar*erreurLidar-coeff_Capteur*erreur_capteur;
		int alphaG = -coeff_Lidar*erreurLidar+coeff_Capteur*erreur_capteur;
 */

void TaskEDGE(void * pvParameters){
	for (;;) {

		ulTaskNotifyTake(pdTRUE, portMAX_DELAY);
		Motor_Forward_R(0);
		Motor_Forward_L(0);
		HAL_Delay(10);
		while((capteur_D||capteur_G)==1){

			Motor_Reverse_R(50);
			Motor_Reverse_L(50);
			HAL_Delay(100);
			Motor_Reverse_R(50);
			Motor_Reverse_L(0);
			HAL_Delay(500);
		}
		//s'arreter, reculer, tourner et repartir

	}
}


/* USER CODE END 0 */

/**
 * @brief  The application entry point.
 * @retval int
 */
int main(void)
{

	/* MCU Configuration--------------------------------------------------------*/

	/* Reset of all peripherals, Initializes the Flash interface and the Systick. */
	HAL_Init();

	/* Configure the system clock */
	SystemClock_Config();

	/* Initialize all configured peripherals */
	MX_GPIO_Init();
	MX_DMA_Init();
	MX_SPI2_Init();
	MX_TIM1_Init();
	MX_TIM2_Init();
	MX_TIM3_Init();
	MX_TIM4_Init();
	MX_USART2_UART_Init();
	MX_USART3_UART_Init();
	/* USER CODE BEGIN 2 */
	Start_Motors();
	Motor_Forward_R(50);
	Motor_Forward_L(50);
	ADXL343_Init();
	LIDAR_Init(&hlidar);
	LIDAR_Start(&hlidar);

	ret = xTaskCreate(TaskETAT,"TaskETAT",STACK_SIZE,(void *) NULL,5,&xHandleETAT);
	if (ret != pdPASS)
	{
		printf("Error creating TaskETAT\r\n");
		Error_Handler();
	}
	printf("Task ETAT created\r\n");

	/*
	ret = xTaskCreate(TaskLIDAR,"TaskLIDAR",STACK_SIZE,(void *) NULL,3,&xHandleLIDAR);
	if (ret != pdPASS)
	{
		printf("Error creating TaskLIDAR\r\n");
		Error_Handler();
	}
	printf("Task LIDAR created\r\n");
	 */

	ret = xTaskCreate(TaskMOTOR,"TaskMOTOR",STACK_SIZE,(void *) NULL,3,&xHandleMOTOR);
	if (ret != pdPASS)
	{
		printf("Error creating TaskMOTOR\r\n");
		Error_Handler();
	}
	printf("Task MOTOR created\r\n");


	ret = xTaskCreate(TaskEDGE,"TaskEDGE",STACK_SIZE,(void *) NULL,4,&xHandleEDGE);
	if (ret != pdPASS)
	{
		printf("Error creating TaskEDGE\r\n");
		Error_Handler();
	}
	printf("Task EDGE created\r\n");

	SemDMAHalfCallBack = xSemaphoreCreateBinary();
	SemDMAClpCallBack = xSemaphoreCreateBinary();
	xShockSemaphore = xSemaphoreCreateBinary();
	SemEtat = xSemaphoreCreateBinary();
	//xNoSignalSemaphore = xSemaphoreCreateBinary();
	/* USER CODE END 2 */

	/* Call init function for freertos objects (in cmsis_os2.c) */
	MX_FREERTOS_Init();

	/* Start scheduler */
	osKernelStart();

	/* We should never get here as control is now taken by the scheduler */

	/* Infinite loop */
	/* USER CODE BEGIN WHILE */
	while (1)
	{

		/* USER CODE END WHILE */

		/* USER CODE BEGIN 3 */
	}
	/* USER CODE END 3 */
}

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
/* USER CODE BEGIN 4 */
void HAL_GPIO_EXTI_Callback(uint16_t GPIO_Pin) {

	if (GPIO_Pin == INT1_ACC_Pin) {
		BaseType_t xHigherPriorityTaskWoken = pdFALSE;
		vTaskNotifyGiveFromISR(xHandleETAT, &xHigherPriorityTaskWoken);
		portYIELD_FROM_ISR(xHigherPriorityTaskWoken);
		HAL_GPIO_TogglePin(GPIOC, Status_LED_Pin);
	}
	if (GPIO_Pin == CAPTEUR_D_Pin) {
		if(capteur_D==1){
			capteur_D=0;
		}
		else{
			capteur_D=1;
		}
		printf("capteurD\r\n");
		BaseType_t xHigherPriorityTaskWoken = pdFALSE;
		vTaskNotifyGiveFromISR(xHandleEDGE, &xHigherPriorityTaskWoken);
		portYIELD_FROM_ISR(xHigherPriorityTaskWoken);
	}
	if (GPIO_Pin == CAPTEUR_G_Pin) {
		if(capteur_G==1){
			capteur_G=0;
		}
		else{
			capteur_G=1;
		}
		printf("capteurG\r\n");
		BaseType_t xHigherPriorityTaskWoken = pdFALSE;
		vTaskNotifyGiveFromISR(xHandleEDGE, &xHigherPriorityTaskWoken);
		portYIELD_FROM_ISR(xHigherPriorityTaskWoken);
	}
}
/*
void HAL_UART_RxHalfCpltCallback(UART_HandleTypeDef *huart)
{
	BaseType_t higher_priority_task_woken = pdFALSE;
	xSemaphoreGiveFromISR(SemHalfCallBack,&higher_priority_task_woken);
	portYIELD_FROM_ISR(higher_priority_task_woken);
}

void HAL_UART_RxCpltCallback(UART_HandleTypeDef *huart)
{
	BaseType_t higher_priority_task_woken = pdFALSE;
	xSemaphoreGiveFromISR(SemClpCallBack,&higher_priority_task_woken);
	portYIELD_FROM_ISR(higher_priority_task_woken);
}
 */
/* USER CODE END 4 */
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


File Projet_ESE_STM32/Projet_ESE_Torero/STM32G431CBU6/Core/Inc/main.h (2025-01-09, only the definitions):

#define INT2_ACC_Pin GPIO_PIN_13
#define INT2_ACC_GPIO_Port GPIOC
#define INT2_ACC_EXTI_IRQn EXTI15_10_IRQn
#define RESET_Pin GPIO_PIN_10
#define RESET_GPIO_Port GPIOG
#define CS_ACC_Pin GPIO_PIN_5
#define CS_ACC_GPIO_Port GPIOA
#define LED_NE_Pin GPIO_PIN_7
#define LED_NE_GPIO_Port GPIOA
#define LED_SE_Pin GPIO_PIN_4
#define LED_SE_GPIO_Port GPIOC
#define CAPTEUR_G_Pin GPIO_PIN_0
#define CAPTEUR_G_GPIO_Port GPIOB
#define CAPTEUR_G_EXTI_IRQn EXTI0_IRQn
#define CAPTEUR_D_Pin GPIO_PIN_1
#define CAPTEUR_D_GPIO_Port GPIOB
#define CAPTEUR_D_EXTI_IRQn EXTI1_IRQn
#define M_EN_LIDAR_Pin GPIO_PIN_2
#define M_EN_LIDAR_GPIO_Port GPIOB
#define USART3_TX_LIDAR_Pin GPIO_PIN_10
#define USART3_TX_LIDAR_GPIO_Port GPIOB
#define USART3_RX_LIDAR_Pin GPIO_PIN_11
#define USART3_RX_LIDAR_GPIO_Port GPIOB
#define LED_NW_Pin GPIO_PIN_12
#define LED_NW_GPIO_Port GPIOB
#define SPI2_SCK_TO_SCLK_ACC_Pin GPIO_PIN_13
#define SPI2_SCK_TO_SCLK_ACC_GPIO_Port GPIOB
#define SPI2_MISO_TO_SDO_ACC_Pin GPIO_PIN_14
#define SPI2_MISO_TO_SDO_ACC_GPIO_Port GPIOB
#define SPI2_MOSI_TO_SDI_ACC_Pin GPIO_PIN_15
#define SPI2_MOSI_TO_SDI_ACC_GPIO_Port GPIOB
#define LED_SW_Pin GPIO_PIN_6
#define LED_SW_GPIO_Port GPIOC
#define INT1_ACC_Pin GPIO_PIN_10
#define INT1_ACC_GPIO_Port GPIOA
#define INT1_ACC_EXTI_IRQn EXTI15_10_IRQn
#define DEV_EN_LIDAR_Pin GPIO_PIN_15
#define DEV_EN_LIDAR_GPIO_Port GPIOA
#define Status_LED_Pin GPIO_PIN_10
#define Status_LED_GPIO_Port GPIOC
#define Status_LED_debbug_Pin GPIO_PIN_11
#define Status_LED_debbug_GPIO_Port GPIOC
#define LED_W_Pin GPIO_PIN_4
#define LED_W_GPIO_Port GPIOB
#define LED_N_Pin GPIO_PIN_5
#define LED_N_GPIO_Port GPIOB
#define LED_E_Pin GPIO_PIN_6
#define LED_E_GPIO_Port GPIOB
#define LED_S_Pin GPIO_PIN_7
#define LED_S_GPIO_Port GPIOB
#define TIM4_CH4_M_SCTR_LIDAR_Pin GPIO_PIN_9
#define TIM4_CH4_M_SCTR_LIDAR_GPIO_Port GPIOB

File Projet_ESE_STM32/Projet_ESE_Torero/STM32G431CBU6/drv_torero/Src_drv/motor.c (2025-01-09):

#include "tim.h"
#include "motor.h"

#define PWM_MAX_DUTY_CYCLE 40
#define FWD_GPIO_PIN_R GPIO_PIN_8  // PA8 -> FWD
#define REV_GPIO_PIN_R GPIO_PIN_9  // PA9 -> REV
#define FWD_GPIO_PIN_L GPIO_PIN_0  // PA0 -> FWD
#define REV_GPIO_PIN_L GPIO_PIN_1  // PA1 -> REV
#define FWD_GPIO_PORT_R GPIOA      // Port pour FWD_R
#define REV_GPIO_PORT_R GPIOA      // Port pour REV_R
#define FWD_GPIO_PORT_L GPIOA      // Port pour FWD_L
#define REV_GPIO_PORT_L GPIOA      // Port pour REV_L
#define UART_RX_BUFFER_SIZE 1
#define UART_TX_BUFFER_SIZE 64

void Motor_Forward_R(int percentage) {
    // Limiter le pourcentage entre 0 et 100
    if (percentage > 100) percentage = 100;
    if (percentage < 0) percentage = 0;

    // Mettre à jour les GPIO et PWM pour avancer (moteur droit)
    HAL_GPIO_WritePin(REV_GPIO_PORT_R, REV_GPIO_PIN_R, GPIO_PIN_RESET);
    HAL_GPIO_WritePin(FWD_GPIO_PORT_R, FWD_GPIO_PIN_R, GPIO_PIN_SET);
    TIM1->CCR1 = 0;
    TIM1->CCR2 = (percentage * PWM_MAX_DUTY_CYCLE) / 100;
}

void Motor_Reverse_R(int percentage) {
    // Limiter le pourcentage entre 0 et 100
    if (percentage > 100) percentage = 100;
    if (percentage < 0) percentage = 0;

    // Mettre à jour les GPIO et PWM pour reculer (moteur droit)
    HAL_GPIO_WritePin(FWD_GPIO_PORT_R, FWD_GPIO_PIN_R, GPIO_PIN_RESET);
    HAL_GPIO_WritePin(REV_GPIO_PORT_R, REV_GPIO_PIN_R, GPIO_PIN_SET);
    TIM1->CCR1 = (percentage * PWM_MAX_DUTY_CYCLE) / 100;
    TIM1->CCR2 = 0;
}

void Motor_Forward_L(int percentage) {
    // Limiter le pourcentage entre 0 et 100
    if (percentage > 100) percentage = 100;
    if (percentage < 0) percentage = 0;

    // Mettre à jour les GPIO et PWM pour avancer (moteur gauche)
    HAL_GPIO_WritePin(REV_GPIO_PORT_L, REV_GPIO_PIN_L, GPIO_PIN_RESET);
    HAL_GPIO_WritePin(FWD_GPIO_PORT_L, FWD_GPIO_PIN_L, GPIO_PIN_SET);
    TIM2->CCR1 = (percentage * PWM_MAX_DUTY_CYCLE) / 100;
    TIM2->CCR2 = 0;
}

void Motor_Reverse_L(int percentage) {
    // Limiter le pourcentage entre 0 et 100
    if (percentage > 100) percentage = 100;
    if (percentage < 0) percentage = 0;

    // Mettre à jour les GPIO et PWM pour reculer (moteur gauche)
    HAL_GPIO_WritePin(FWD_GPIO_PORT_L, FWD_GPIO_PIN_L, GPIO_PIN_RESET);
    HAL_GPIO_WritePin(REV_GPIO_PORT_L, REV_GPIO_PIN_L, GPIO_PIN_SET);
    TIM2->CCR1 = 0;
    TIM2->CCR2 = (percentage * PWM_MAX_DUTY_CYCLE) / 100;
}

void Stop_Motors(void) {
    HAL_TIM_PWM_Stop(&htim1, TIM_CHANNEL_1);
    HAL_TIM_PWM_Stop(&htim1, TIM_CHANNEL_2);
    HAL_TIM_PWM_Start(&htim2, TIM_CHANNEL_1);
    HAL_TIM_PWM_Start(&htim2, TIM_CHANNEL_2);
    TIM1->CCR1 = 0;
    TIM1->CCR2 = 0;
    TIM2->CCR1 = 0;
    TIM2->CCR2 = 0;
}

void Start_Motors(void) {
    HAL_TIM_PWM_Start(&htim1, TIM_CHANNEL_1);
    HAL_TIM_PWM_Start(&htim1, TIM_CHANNEL_2);
    HAL_TIM_PWM_Start(&htim2, TIM_CHANNEL_1);
    HAL_TIM_PWM_Start(&htim2, TIM_CHANNEL_2);
    TIM1->CCR1 = 0;
    TIM1->CCR2 = 0;
    TIM2->CCR1 = 0;
    TIM2->CCR2 = 0;
}
int32_t Read_Encoder(TIM_HandleTypeDef *htim) {
    return __HAL_TIM_GET_COUNTER(htim); // Lire la valeur actuelle du compteur
}

void Reset_Encoder(TIM_HandleTypeDef *htim) {
    __HAL_TIM_SET_COUNTER(htim, 0);    // Réinitialiser le compteur
}

void Motor_SetSpeed_R(int percentage) {
    static int currentSpeed_R = 0;  // Maintenir la vitesse actuelle (moteur droit)
    int step = (percentage > currentSpeed_R) ? 1 : -1; // Déterminer le pas (incrément ou décrément)

    // Limiter la cible au pourcentage maximal autorisé
    if (percentage > 100) percentage = 100;
    if (percentage < -100) percentage = -100;

    // Effectuer un ramp-up ou ramp-down jusqu'à la vitesse cible
    while (currentSpeed_R != percentage) {
        currentSpeed_R += step;

        if (currentSpeed_R > 0) {
            // Motor Forward
            HAL_GPIO_WritePin(REV_GPIO_PORT_R, REV_GPIO_PIN_R, GPIO_PIN_RESET); // Stop Reverse
            HAL_GPIO_WritePin(FWD_GPIO_PORT_R, FWD_GPIO_PIN_R, GPIO_PIN_SET);   // Start Forward
            TIM1->CCR2 = (PWM_MAX_DUTY_CYCLE * currentSpeed_R) / 100;           // Ajuster le rapport cyclique sur CCR1
        } else if (currentSpeed_R < 0) {
            // Motor Reverse
            HAL_GPIO_WritePin(FWD_GPIO_PORT_R, FWD_GPIO_PIN_R, GPIO_PIN_RESET); // Stop Forward
            HAL_GPIO_WritePin(REV_GPIO_PORT_R, REV_GPIO_PIN_R, GPIO_PIN_SET);   // Start Reverse
            TIM1->CCR1 = (PWM_MAX_DUTY_CYCLE * -currentSpeed_R) / 100;          // Ajuster le rapport cyclique sur CCR2
        } else {
            // Stop both directions
            HAL_GPIO_WritePin(FWD_GPIO_PORT_R, FWD_GPIO_PIN_R, GPIO_PIN_RESET);
            HAL_GPIO_WritePin(REV_GPIO_PORT_R, REV_GPIO_PIN_R, GPIO_PIN_RESET);
            TIM1->CCR1 = 0;  // Désactiver Forward
            TIM1->CCR2 = 0;  // Désactiver Reverse
        }

        // Délai pour un changement progressif
        HAL_Delay(10);
    }
}

void Motor_SetSpeed_L(int percentage) {
    static int currentSpeed_L = 0;  // Maintenir la vitesse actuelle (moteur gauche)
    int step = (percentage > currentSpeed_L) ? 1 : -1; // Déterminer le pas (incrément ou décrément)

    // Limiter la cible au pourcentage maximal autorisé
    if (percentage > 100) percentage = 100;
    if (percentage < -100) percentage = -100;

    // Effectuer un ramp-up ou ramp-down jusqu'à la vitesse cible
    while (currentSpeed_L != percentage) {
        currentSpeed_L += step;

        if (currentSpeed_L > 0) {
            // Motor Forward
            HAL_GPIO_WritePin(REV_GPIO_PORT_L, REV_GPIO_PIN_L, GPIO_PIN_RESET); // Stop Reverse
            HAL_GPIO_WritePin(FWD_GPIO_PORT_L, FWD_GPIO_PIN_L, GPIO_PIN_SET);   // Start Forward
            TIM2->CCR1 = (PWM_MAX_DUTY_CYCLE * currentSpeed_L) / 100;           // Ajuster le rapport cyclique sur CCR1
        } else if (currentSpeed_L < 0) {
            // Motor Reverse
            HAL_GPIO_WritePin(FWD_GPIO_PORT_L, FWD_GPIO_PIN_L, GPIO_PIN_RESET); // Stop Forward
            HAL_GPIO_WritePin(REV_GPIO_PORT_L, REV_GPIO_PIN_L, GPIO_PIN_SET);   // Start Reverse
            TIM2->CCR2 = (PWM_MAX_DUTY_CYCLE * -currentSpeed_L) / 100;          // Ajuster le rapport cyclique sur CCR2
        } else {
            // Stop both directions
            HAL_GPIO_WritePin(FWD_GPIO_PORT_L, FWD_GPIO_PIN_L, GPIO_PIN_RESET);
            HAL_GPIO_WritePin(REV_GPIO_PORT_L, REV_GPIO_PIN_L, GPIO_PIN_RESET);
            TIM2->CCR1 = 0;  // Désactiver Forward
            TIM2->CCR2 = 0;  // Désactiver Reverse
        }

        // Délai pour un changement progressif
        HAL_Delay(10);
    }
}

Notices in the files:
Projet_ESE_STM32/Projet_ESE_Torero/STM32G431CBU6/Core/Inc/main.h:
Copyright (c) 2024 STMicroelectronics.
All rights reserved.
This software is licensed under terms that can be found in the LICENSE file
